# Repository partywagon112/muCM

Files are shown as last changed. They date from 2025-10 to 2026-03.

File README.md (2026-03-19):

# μCM

A small ESP32 based flexible controller, intended for Matter to control an RGB light or motor, but very very flexible. Based around ESP32-C6 for flexibility. Built to work in two contexts, in isolated locations where only power may be provided, up to 40V 3A, or as a PD powered dongle, up to 20V, 3A. 

Includes a 3V3 CAN driver for interacting with smaller devices, two pairs of half bridges allow driving servos, LEDs, or outputs more generally. 

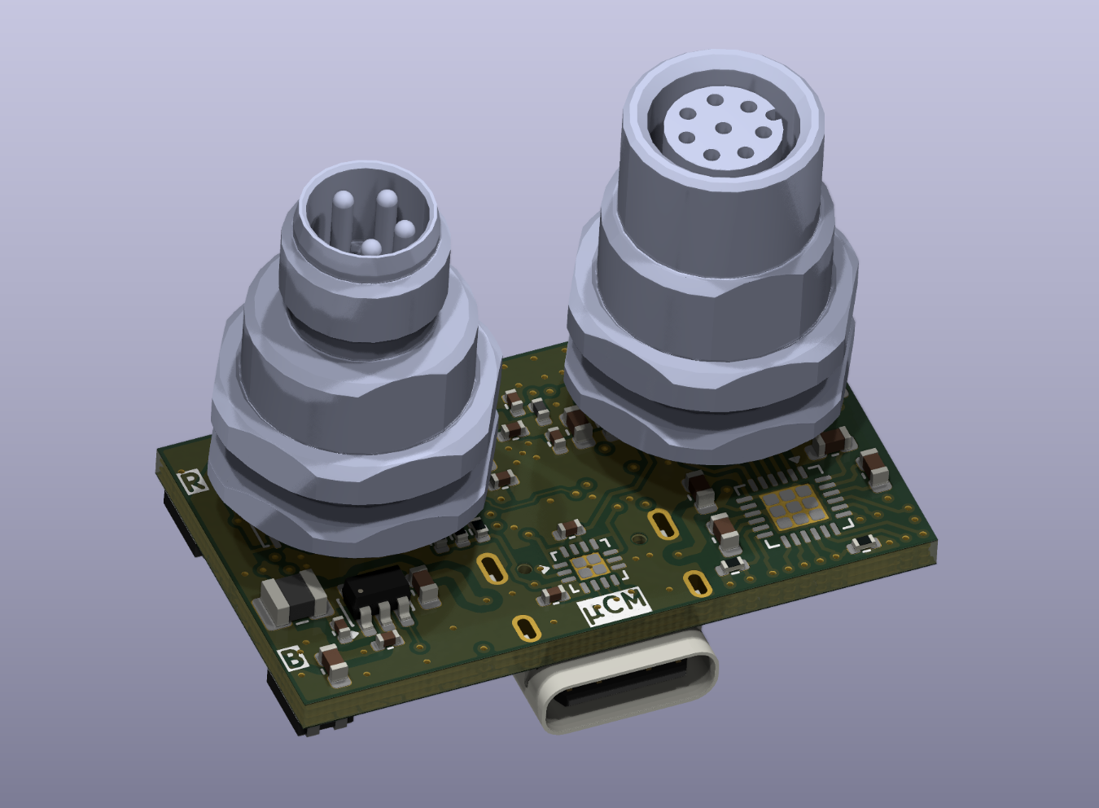
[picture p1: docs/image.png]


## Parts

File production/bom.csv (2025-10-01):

Designator | Footprint | Quantity | Value | LCSC Part #
C1 | 0805 | 1 | 22nF | KAS21KR71H223KU
C10, C11, C12, C14, C7, C9 | 0603 | 6 | 10 nF | GCM188R71H103KA37D
C13, C17, C28, C30, C6, C8 | 0402 | 6 | 100n | GCM155R71H104KE02J
C15, C16 | 0402 | 2 | 5.6n | GCM155R71H562KA55D
C2, C31 | 0603 | 2 | 220nF | GCM188R71H224KA64D
C29 | 0805 | 1 | 10uF | CGA4J1X7S1C106K125AE
C3, C5 | 0805 | 2 | 100n | KAS21KR72A104KU
C4 | 0603 | 1 | 1u | GRT188R61H105KE13D
D1 | SOT-416 | 1 | RCLAMP0582B.TCT | RCLAMP0582B.TCT
D2, D3 | Nexperia_CFP3_SOD-123W | 2 | PMEG60T30ELRX | PMEG60T30ELRX
F1 | 0805 | 1 | 5A | MFU0805FF05000P100
J1 | USB_C_Receptacle_GCT_USB4105-xx-A_16P_TopMnt_Horizontal | 1 | USB4105 | USB4105-GF-A
J2 | JST_PH_S4B-PH-K_1x04_P2.00mm_Horizontal | 1 | S4B-PH-K-S | S4B-PH-K-S
J4 | JST_XH_S2B-XH-A-1_1x02_P2.50mm_Horizontal | 1 | S2B-XH-A-1 | S2B-XH-A-1
J5 | JST_PH_S2B-PH-K_1x02_P2.00mm_Horizontal | 1 | S2B-PH-K-S | S2B-PH-K-S
L2 | 1008 | 1 | 6.8 uH | SRN2510BTA-6R8M
LED1, LED2 | 0603 | 2 | Red | 150060SS75020
R1, R5, R6, R7, R8 | 0402 | 5 | 10k | CR0402AFX-1002GAS
R10, R11, R9 | 0402 | 3 | 4.75k | CR0402AFX-4751GAS
R2, R3 | 0402 | 2 | 2k | CR0402AFX-2001GAS
R4 | 0402 | 1 | 330 kR | CRGCQ0402F330K
SW1, SW2 | SW_Push_1P1T-SH_NO_CK_KMR2xxG | 2 | NO | KMR221G LFS
U1 | WQFN-14-1EP_2.5x2.5mm_P0.5mm_EP1.45x1.45mm | 1 | FUSB302B01MPX | FUSB302B01MPX
U2 | ESP32-S3-WROOM-1 | 1 | ESP32-S3-WROOM-1-N8R8 | ESP32-S3-WROOM-1-N8R8
U3 | VQFN-24-1EP_4x4mm_P0.5mm_EP2.45x2.45mm | 1 | DRV8955 | DRV8955PRGER
U5 | SOT-23-6 | 1 | LMR50410Y3FQDBVRQ1 | LMR50410Y3FQDBVRQ1

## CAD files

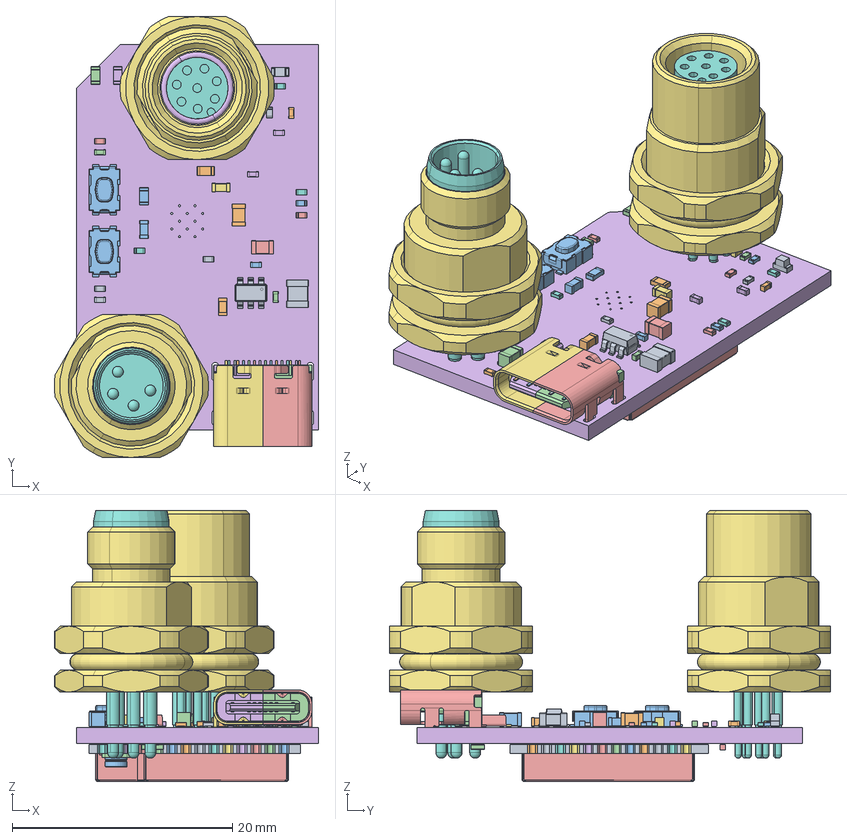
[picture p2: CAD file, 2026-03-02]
housing/MatterRGB_Assy.FCStd
24.0 x 40.0 x 24.6 mm
LED_0603_1608Metric
C_0603_1608Metric
C_0603_1608Metric001
USB_C_Receptacle_GCT_USB4105-xx-A_16P_TopMnt_Horizontal
USB_C_Receptacle_GCT_USB4105-xx-A_16P_TopMnt_Horizontal001
USB_C_Receptacle_GCT_USB4105-xx-A_16P_TopMnt_Horizontal002
USB_C_Receptacle_GCT_USB4105-xx-A_16P_TopMnt_Horizontal003
USB_C_Receptacle_GCT_USB4105-xx-A_16P_TopMnt_Horizontal004
USB_C_Receptacle_GCT_USB4105-xx-A_16P_TopMnt_Horizontal005
USB_C_Receptacle_GCT_USB4105-xx-A_16P_TopMnt_Horizontal006
USB_C_Receptacle_GCT_USB4105-xx-A_16P_TopMnt_Horizontal007
USB_C_Receptacle_GCT_USB4105-xx-A_16P_TopMnt_Horizontal008
USB_C_Receptacle_GCT_USB4105-xx-A_16P_TopMnt_Horizontal009
USB_C_Receptacle_GCT_USB4105-xx-A_16P_TopMnt_Horizontal010
USB_C_Receptacle_GCT_USB4105-xx-A_16P_TopMnt_Horizontal011
USB_C_Receptacle_GCT_USB4105-xx-A_16P_TopMnt_Horizontal012
USB_C_Receptacle_GCT_USB4105-xx-A_16P_TopMnt_Horizontal013
USB_C_Receptacle_GCT_USB4105-xx-A_16P_TopMnt_Horizontal014
USB_C_Receptacle_GCT_USB4105-xx-A_16P_TopMnt_Horizontal015
USB_C_Receptacle_GCT_USB4105-xx-A_16P_TopMnt_Horizontal016
USB_C_Receptacle_GCT_USB4105-xx-A_16P_TopMnt_Horizontal017
USB_C_Receptacle_GCT_USB4105-xx-A_16P_TopMnt_Horizontal018
USB_C_Receptacle_GCT_USB4105-xx-A_16P_TopMnt_Horizontal019
USB_C_Receptacle_GCT_USB4105-xx-A_16P_TopMnt_Horizontal020
USB_C_Receptacle_GCT_USB4105-xx-A_16P_TopMnt_Horizontal021
USB_C_Receptacle_GCT_USB4105-xx-A_16P_TopMnt_Horizontal022
USB_C_Receptacle_GCT_USB4105-xx-A_16P_TopMnt_Horizontal023
USB_C_Receptacle_GCT_USB4105-xx-A_16P_TopMnt_Horizontal024
USB_C_Receptacle_GCT_USB4105-xx-A_16P_TopMnt_Horizontal025
USB_C_Receptacle_GCT_USB4105-xx-A_16P_TopMnt_Horizontal026
USB_C_Receptacle_GCT_USB4105-xx-A_16P_TopMnt_Horizontal027
USB_C_Receptacle_GCT_USB4105-xx-A_16P_TopMnt_Horizontal028
USB_C_Receptacle_GCT_USB4105-xx-A_16P_TopMnt_Horizontal029
USB_C_Receptacle_GCT_USB4105-xx-A_16P_TopMnt_Horizontal030
USB_C_Receptacle_GCT_USB4105-xx-A_16P_TopMnt_Horizontal031
USB_C_Receptacle_GCT_USB4105-xx-A_16P_TopMnt_Horizontal032
USB_C_Receptacle_GCT_USB4105-xx-A_16P_TopMnt_Horizontal033
USB_C_Receptacle_GCT_USB4105-xx-A_16P_TopMnt_Horizontal034
USB_C_Receptacle_GCT_USB4105-xx-A_16P_TopMnt_Horizontal035
R_0402_1005Metric
C_0402_1005Metric
C_0805_2012Metric
R_0402_1005Metric001
R_0603_1608Metric
R_0402_1005Metric002
C_0402_1005Metric001
CDM806 HOUSING
M8_PINS_MALE_FRONT_4P
L_1008_2520Metric
R_0603_1608Metric001
R_0402_1005Metric003
R_0402_1005Metric004
R_0402_1005Metric005
R_0603_1608Metric002
C_0402_1005Metric002
R_0402_1005Metric006
SOT-23-6
R_0402_1005Metric007
SW_Push_1P1T-SH_NO_CK_KMR2xxG
C_0805_2012Metric001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

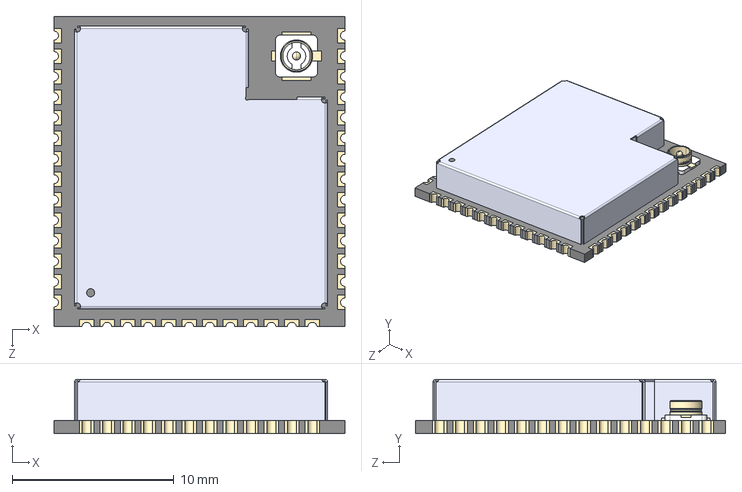
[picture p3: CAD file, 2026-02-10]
hardware/3d/ESP32-S3-WROOM-1U-N8R8--3DModel-STEP-56544.STEP
18.0 x 3.35 x 19.2 mm

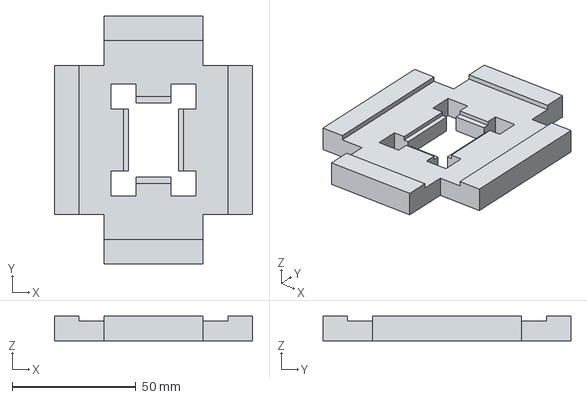
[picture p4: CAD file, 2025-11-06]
production/stencil_holder-Body.step
80.0 x 100.0 x 10.0 mm

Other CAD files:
housing/MatterRGB.step
production/stencil_holder.FCStd

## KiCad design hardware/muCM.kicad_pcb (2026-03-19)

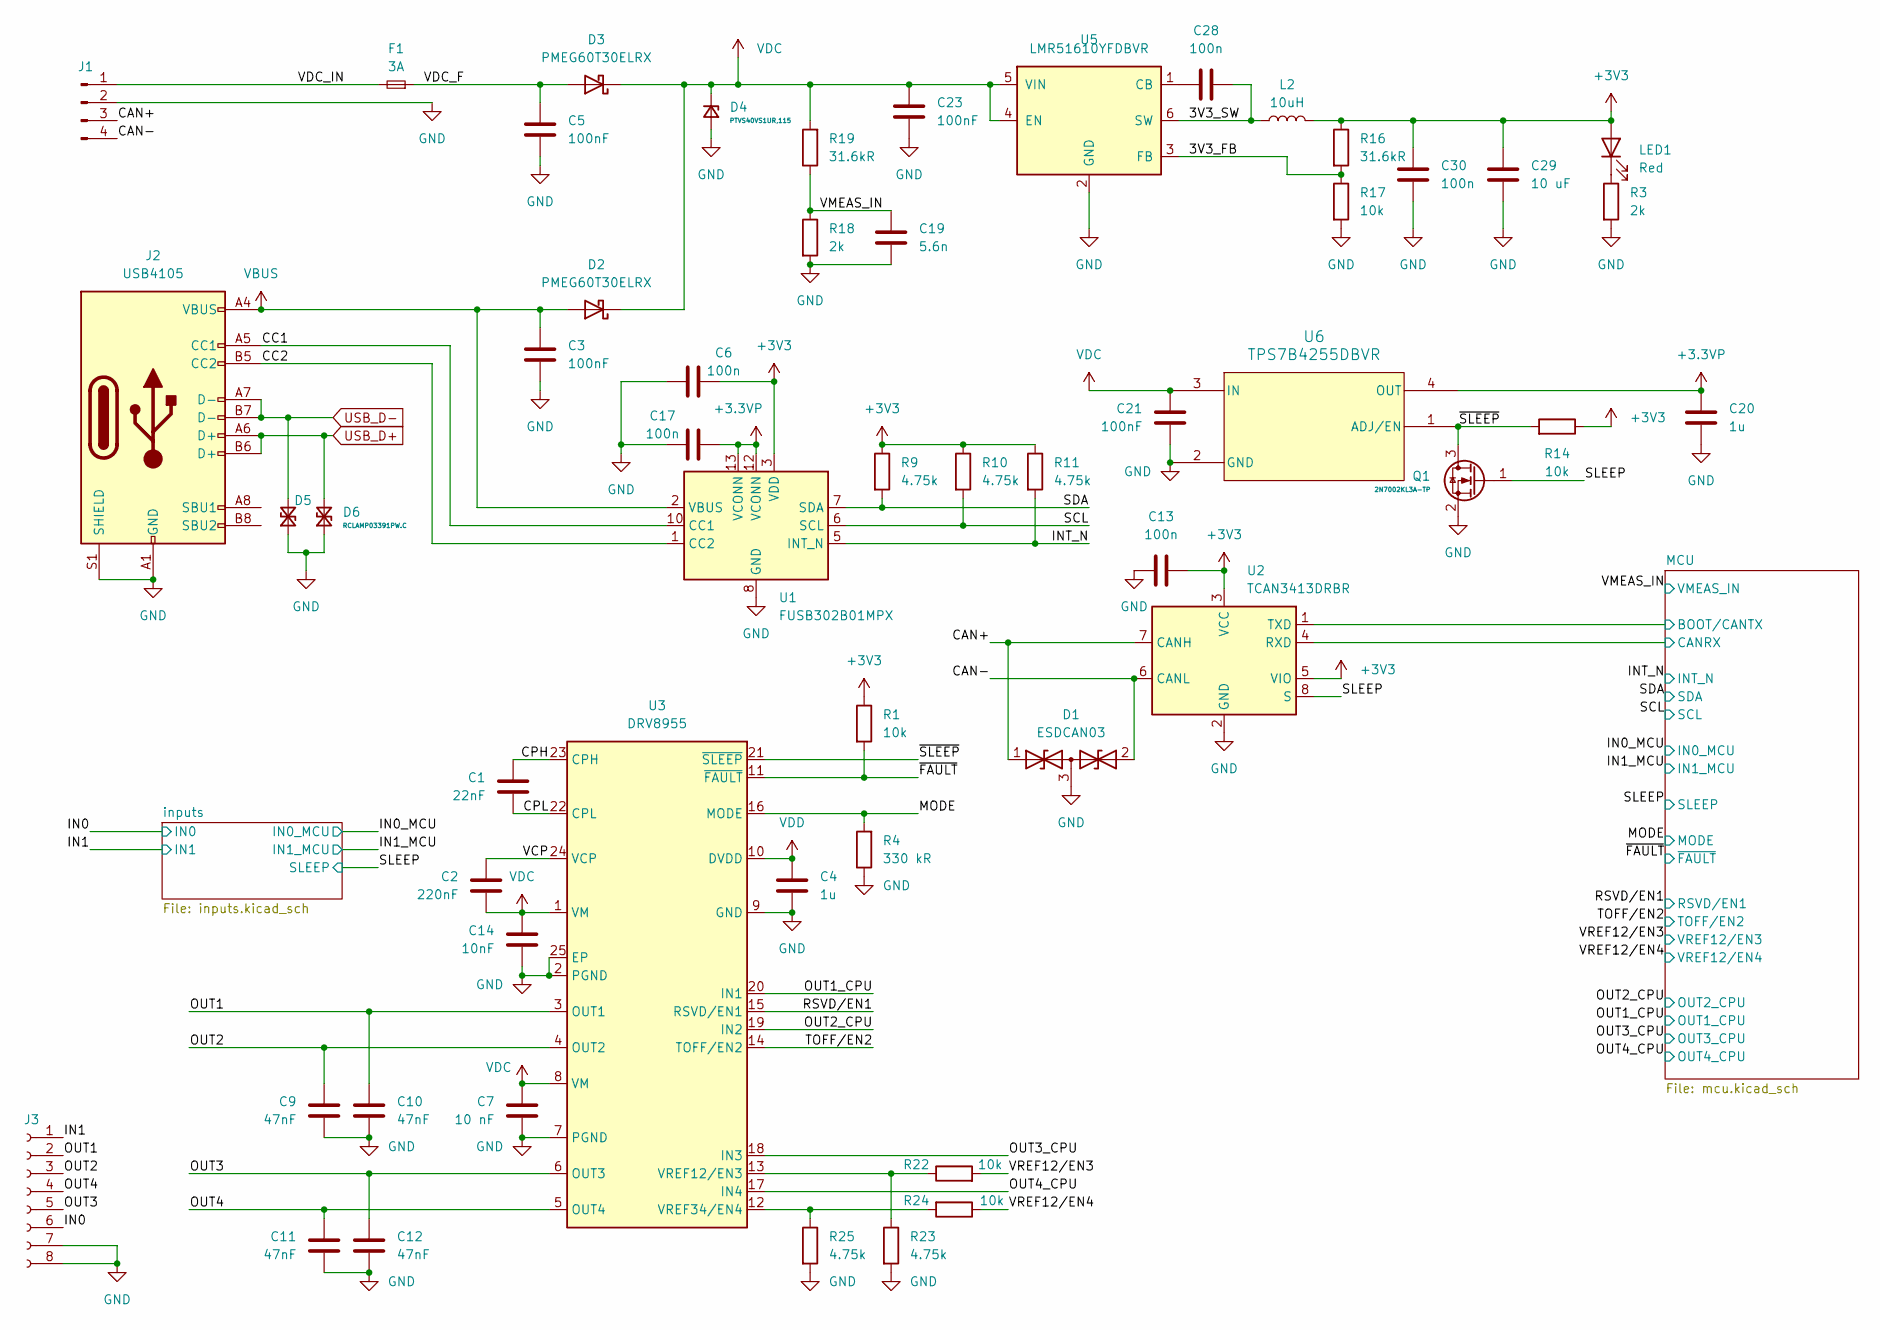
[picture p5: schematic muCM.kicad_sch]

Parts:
C1: 22nF; C_0603_1608Metric; MPN CL10B223KC8WPNC; DigiKey SPN 1276-CL10B223KC8WPNCCT-ND
C2: 220nF; C_0603_1608Metric; MPN HMK107C7224MAHTE; DigiKey SPN 587-5013-1-ND
C3, C5, C21, C23: 100nF; C_0603_1608Metric; MPN GCJ188R72A104KA01D; DigiKey SPN 490-13420-1-ND
C4, C20: 1u; C_0603_1608Metric; MPN GRT188R61H105KE13D; DigiKey SPN 490-12330-1-ND
C6, C13, C17, C28, C30: 100n; C_0402_1005Metric; MPN GCM155R71H104KE02J
C7: 10 nF; R_0603_1608Metric; MPN GCM188R71H103KA37D; DigiKey SPN 490-4778-1-ND
C9, C10, C11, C12: 47nF; C_0603_1608Metric; MPN CGA3E3X7S2A473K080AE; DigiKey SPN 445-173702-1-ND
C14: 10nF; C_0603_1608Metric; MPN CL10B103KC8WPNC; DigiKey SPN 1276-6556-1-ND
C19: 5.6n; C_0402_1005Metric; MPN GCM155R71H562KA55D; DigiKey SPN 490-GCM155R71H562KA55DCT-ND
C29: 10 uF; C_0603_1608Metric; MPN GRT188R61E106ME13D; DigiKey SPN 490-12323-1-ND
D1: ESDCAN03; DFN1006-3; MPN ESDCAN03-2BM3Y; DigiKey SPN 497-ESDCAN03-2BM3YCT-ND
D2, D3: PMEG60T30ELRX; Nexperia_CFP3_SOD-123W; MPN PMEG60T30ELRX; DigiKey SPN 1727-7806-1-ND
D4: PTVS40VS1UR,115; Nexperia_CFP3_SOD-123W; MPN PTVS40VS1UR,115; DigiKey SPN 1727-5873-1-ND
D5, D6: RCLAMP03391PW.C; D_SOD-882; MPN RCLAMP03391PW.C; DigiKey SPN 600-RCLAMP03391PW.CCT-ND
F1: 3A; Fuse_0805_2012Metric; MPN MFU0805FF03000P100; DigiKey SPN MFU08053.00CT-ND
J1: CDM806-04A-MP-F011-67; CUI_CDM806-04A-MP-F011-67; MPN CDM806-04A-MP-F011-67; DigiKey SPN 2223-CDM806-04A-MP-F011-67-ND
J2: USB4105; USB_C_Receptacle_GCT_USB4105-xx-A_16P_TopMnt_Horizontal; MPN USB4105-GF-A; DigiKey SPN 2073-USB4105-GF-ACT-ND
J3: CDM805-08A-FP-F011-67; CUI_CDM805-08A-FP-F011-67; MPN CDM805-08A-FP-F011-67; DigiKey SPN 2223-CDM805-08A-FP-F011-67-ND
L2: 10uH; L_1008_2520Metric; MPN SRN2510BTA-100M; DigiKey SPN 118-SRN2510BTA-100MCT-ND
LED1: Red; LED_0603_1608Metric; MPN 150060SS75020
Q1: 2N7002KL3A-TP; Diodes_DFN1006-3; MPN 2N7002KL3A-TP; DigiKey SPN 353-2N7002KL3A-TPCT-ND
R1, R14, R17, R22, R24: 10k; R_0402_1005Metric; MPN CR0402AFX-1002GAS; DigiKey SPN CR0402AFX-1002GASCT-ND
R3, R18: 2k; R_0402_1005Metric; MPN CR0402AFX-2001GAS
R4: 330 kR; R_0402_1005Metric; MPN CRGCQ0402F330K; DigiKey SPN A129657CT-ND
R9, R10, R11, R23, R25: 4.75k; R_0402_1005Metric; MPN CR0402AFX-4751GAS; DigiKey SPN CR0402AFX-4751GASCT-ND
R16, R19: 31.6kR; R_0402_1005Metric; MPN CRCW040231K6FKED; DigiKey SPN 541-31.6KLCT-ND
U1: FUSB302B01MPX; WQFN-14-1EP_2.5x2.5mm_P0.5mm_EP1.45x1.45mm; MPN FUSB302B01MPX; DigiKey SPN FUSB302B01MPXCT-ND
U2: TCAN3413DRBR; VSON-8-1EP_3x3mm_P0.65mm_EP1.6x2.4mm; MPN TCAN3413DRBR; DigiKey SPN 296-TCAN3413DRBRCT-ND
U3: DRV8955; VQFN-24-1EP_4x4mm_P0.5mm_EP2.45x2.45mm; MPN DRV8955PRGER; DigiKey SPN 296-DRV8955PRGERCT-ND
U5: LMR51610YFDBVR; SOT-23-6; MPN LMR51610YFDBVR; DigiKey SPN 296-LMR51610YFDBVRCT-ND
U6: TPS7B4255DBVR; SOT-23-5; MPN TPS7B4255DBVR; DigiKey SPN 296-TPS7B4255DBVRCT-ND

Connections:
+3.3VP: C17.1, C20.1, U1.12 (VCONN), U1.13 (VCONN), U6.4 (OUT); also elsewhere on the board
+3V3: C6.1, C13.2, C29.1, C30.1, L2.2, LED1.2 (A), R1.1, R9.1, R10.1, R11.1, R14.1, R16.1, U1.3 (VDD), U1.4 (VDD), U2.3 (VCC), U2.5 (VIO); also elsewhere on the board
/3V3_FB: R16.2, R17.1, U5.3 (FB)
/3V3_SW: C28.2, L2.1, U5.6 (SW)
/CAN+: D1.1 (A1), J1.3, U2.7 (CANH)
/CAN-: D1.2 (A2), J1.4, U2.6 (CANL)
/CC1: J2.A5 (CC1), U1.10 (CC1), U1.11 (CC1)
/CC2: J2.B5 (CC2), U1.1 (CC2), U1.14 (CC2)
/CPH: C1.1, U3.23 (CPH)
/CPL: C1.2, U3.22 (CPL)
/IN0: J3.6; also elsewhere on the board
/IN1: J3.1; also elsewhere on the board
/INT_N: R11.2, U1.5 (INT_N); also elsewhere on the board
/MCU/BOOT/CANTX: U2.1 (TXD); also elsewhere on the board
/MCU/CANRX: U2.4 (RXD); also elsewhere on the board
/MODE: R4.2, U3.16 (MODE); also elsewhere on the board
/OUT1: C10.1, J3.2, U3.3 (OUT1)
/OUT1_CPU: U3.20 (IN1); also elsewhere on the board
/OUT2: C9.1, J3.3, U3.4 (OUT2)
/OUT2_CPU: U3.19 (IN2); also elsewhere on the board
/OUT3: C12.1, J3.5, U3.6 (OUT3)
/OUT3_CPU: U3.18 (IN3); also elsewhere on the board
/OUT4: C11.1, J3.4, U3.5 (OUT4)
/OUT4_CPU: U3.17 (IN4); also elsewhere on the board
/RSVD/EN1: U3.15 (RSVD/EN1); also elsewhere on the board
/SCL: R10.2, U1.6 (SCL); also elsewhere on the board
/SDA: R9.2, U1.7 (SDA); also elsewhere on the board
/SLEEP: Q1.1 (G), U2.8 (S); also elsewhere on the board
/TOFF/EN2: U3.14 (TOFF/EN2); also elsewhere on the board
/VCP: C2.1, U3.24 (VCP)
/VDC_F: C5.1, D3.2 (A), F1.1
/VDC_IN: F1.2, J1.1
/VMEAS_IN: C19.1, R18.1, R19.1; also elsewhere on the board
/VREF12/EN3: R22.2; also elsewhere on the board
/VREF12/EN4: R24.1; also elsewhere on the board
/~FAULT: R1.2, U3.11 (~FAULT); also elsewhere on the board
/~SLEEP: Q1.3 (D), R14.2, U3.21 (~SLEEP), U6.1 (ADJ/EN)
GND: C3.2, C4.2, C5.2, C6.2, C7.2, C9.2, C10.2, C11.2, C12.2, C13.1, C14.2, C17.2, C19.2, C20.2, C21.2, C23.2, C29.2, C30.2, D1.3 (common), D4.2 (A), D5.1 (A1), D6.1 (A1), J1.2, J2.A1 (GND), J2.A12 (GND), J2.B1 (GND), J2.B12 (GND), J2.S1 (SHIELD), J3.7, J3.8, Q1.2 (S), R3.2, R4.1, R17.2, R18.2, R23.2, R25.2, U1.8 (GND), U1.9 (GND), U1.15 (GND), U2.2 (GND), U2.9, U3.2 (PGND), U3.7 (PGND), U3.9 (GND), U3.25 (EP), U5.2 (GND), U6.2 (GND); also elsewhere on the board
unnamed: LED1.1 (K), R3.1
unnamed: R22.1, R23.1, U3.13 (VREF12/EN3)
unnamed: R24.2, R25.1, U3.12 (VREF34/EN4)
unnamed: C28.1, U5.1 (CB)
USB_D+: D6.2 (A2), J2.A6 (D+), J2.B6 (D+); also elsewhere on the board
USB_D-: D5.2 (A2), J2.A7 (D-), J2.B7 (D-); also elsewhere on the board
VBUS: C3.1, D2.2 (A), J2.A4 (VBUS), J2.A9 (VBUS), J2.B4 (VBUS), J2.B9 (VBUS), U1.2 (VBUS)
VDC: C2.2, C7.1, C14.1, C21.1, C23.1, D2.1 (K), D3.1 (K), D4.1 (K), R19.2, U3.1 (VM), U3.8 (VM), U5.4 (EN), U5.5 (VIN), U6.3 (IN)
VDD: C4.1, U3.10 (DVDD)

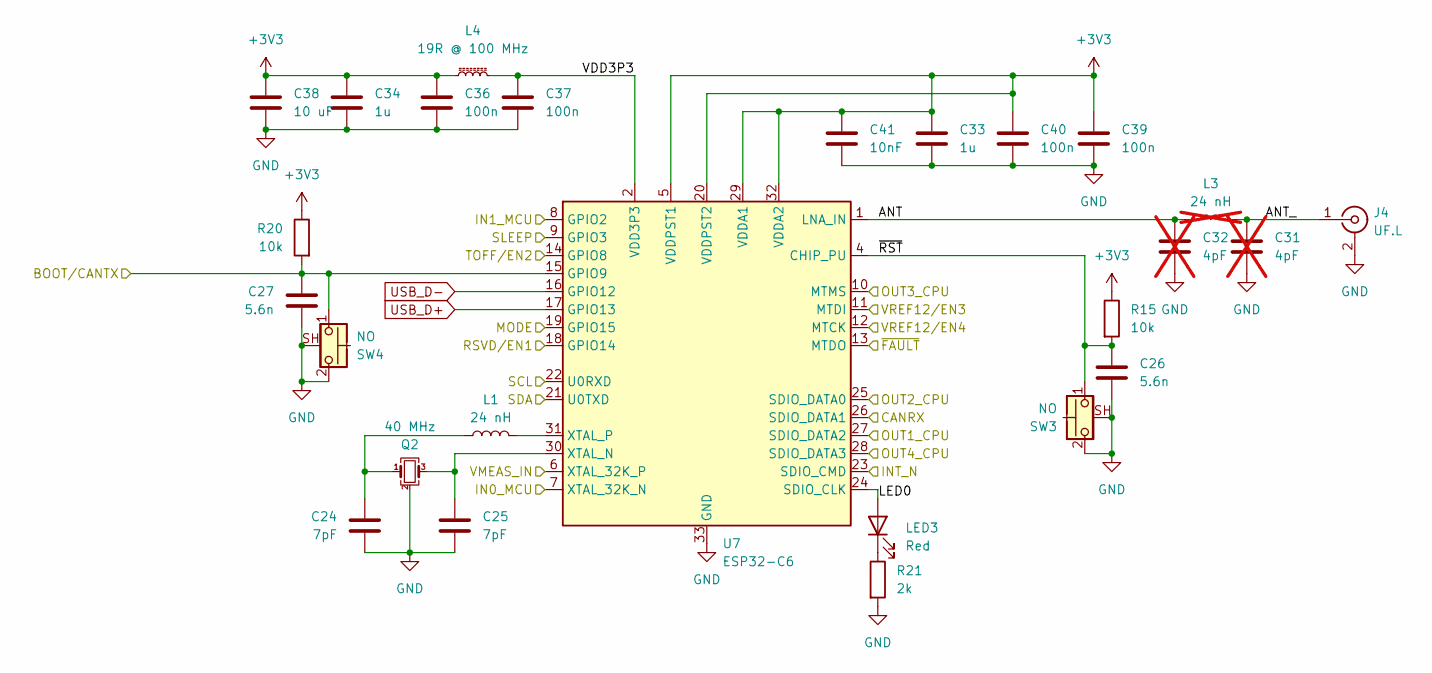
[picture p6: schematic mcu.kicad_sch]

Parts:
C24, C25: 7pF; C_0402_1005Metric; MPN GCM1555C1H7R0BA16D; DigiKey SPN 490-GCM1555C1H7R0BA16DCT-ND
C26, C27: 5.6n; C_0402_1005Metric; MPN GCM155R71H562KA55D; DigiKey SPN 490-GCM155R71H562KA55DCT-ND
C31, C32: 4pF; C_0402_1005Metric; MPN GCM1555C1H4R0BA16D; DigiKey SPN 490-GCM1555C1H4R0BA16DCT-ND; not fitted
C33, C34: 1u; C_0603_1608Metric; MPN GRT188R61H105KE13D; DigiKey SPN 490-12330-1-ND
C36, C37, C39, C40: 100n; C_0402_1005Metric; MPN GCM155R71H104KE02J
C38: 10 uF; C_0603_1608Metric; MPN GRT188R61E106ME13D; DigiKey SPN 490-12323-1-ND
C41: 10nF; C_0402_1005Metric; MPN GCM155R71H103KA55D; DigiKey SPN 490-4762-1-ND
J4: UF.L; U.FL_Hirose_U.FL-R-SMT-1_Vertical; MPN U.FL-R-SMT(10); DigiKey SPN H9161CT-ND
L1: 24 nH; L_0402_1005Metric; MPN MLG1005S24NJTD25; DigiKey SPN 445-16275-1-ND
L3: 24 nH; L_0402_1005Metric; MPN MLG1005S24NJTD25; DigiKey SPN 445-16275-1-ND; not fitted
L4: 19R @ 100 MHz; L_0402_1005Metric; MPN LI0402E190R-10; DigiKey SPN 240-LI0402E190R-10CT-ND
LED3: Red; LED_0603_1608Metric; MPN 150060SS75020
Q2: 40 MHz; Crystal_SMD_2016-4Pin_2.0x1.6mm; MPN XTL501100-M118-207; DigiKey SPN 3994-XTL501100-M118-207CT-ND
R15, R20: 10k; R_0402_1005Metric; MPN CR0402AFX-1002GAS; DigiKey SPN CR0402AFX-1002GASCT-ND
R21: 2k; R_0402_1005Metric; MPN CR0402AFX-2001GAS
SW3, SW4: NO; SW_Push_1P1T-SH_NO_CK_KMR2xxG; MPN KMR221G LFS; DigiKey SPN 401-1427-1-ND
U7: ESP32-C6; QFN-32-1EP_5x5mm_P0.5mm_EP3.7x3.7mm; MPN ESP32-C6FH4; DigiKey SPN 1904-ESP32-C6FH4CT-ND

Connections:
+3V3: C33.1, C34.1, C36.1, C38.1, C39.1, C40.1, C41.1, L4.1, R15.1, R20.1, U7.5 (VDDPST1), U7.20 (VDDPST2), U7.29 (VDDA1), U7.32 (VDDA2); also elsewhere on the board
/IN0_MCU: U7.7 (XTAL_32K_N); also elsewhere on the board
/IN1_MCU: U7.8 (GPIO2); also elsewhere on the board
/INT_N: U7.23 (SDIO_CMD); also elsewhere on the board
/MCU/ANT: C32.1, L3.1, U7.1 (LNA_IN)
/MCU/ANT_: C31.1, J4.1 (In), L3.2
/MCU/BOOT/CANTX: C27.1, R20.2, SW4.1, U7.15 (GPIO9); also elsewhere on the board
/MCU/CANRX: U7.26 (SDIO_DATA1); also elsewhere on the board
/MCU/LED0: LED3.2 (A), U7.24 (SDIO_CLK)
/MCU/~RST: C26.1, R15.2, SW3.1, U7.4 (CHIP_PU)
/MODE: U7.19 (GPIO15); also elsewhere on the board
/OUT1_CPU: U7.27 (SDIO_DATA2); also elsewhere on the board
/OUT2_CPU: U7.25 (SDIO_DATA0); also elsewhere on the board
/OUT3_CPU: U7.10 (MTMS); also elsewhere on the board
/OUT4_CPU: U7.28 (SDIO_DATA3); also elsewhere on the board
/RSVD/EN1: U7.18 (GPIO14); also elsewhere on the board
/SCL: U7.22 (U0RXD); also elsewhere on the board
/SDA: U7.21 (U0TXD); also elsewhere on the board
/SLEEP: U7.9 (GPIO3); also elsewhere on the board
/TOFF/EN2: U7.14 (GPIO8); also elsewhere on the board
/VMEAS_IN: U7.6 (XTAL_32K_P); also elsewhere on the board
/VREF12/EN3: U7.11 (MTDI); also elsewhere on the board
/VREF12/EN4: U7.12 (MTCK); also elsewhere on the board
/~FAULT: U7.13 (MTDO); also elsewhere on the board
GND: C24.2, C25.2, C26.2, C27.2, C31.2, C32.2, C33.2, C34.2, C36.2, C37.2, C38.2, C39.2, C40.2, C41.2, J4.2 (Ext), Q2.2 (G), Q2.4 (G), R21.2, SW3.2, SW3.SH (B), SW4.2, SW4.SH (B), U7.33 (GND); also elsewhere on the board
unnamed: C24.1, L1.1, Q2.1
unnamed: LED3.1 (K), R21.1
unnamed: C25.1, Q2.3, U7.30 (XTAL_N)
unnamed: L1.2, U7.31 (XTAL_P)
USB_D+: U7.17 (GPIO13); also elsewhere on the board
USB_D-: U7.16 (GPIO12); also elsewhere on the board
VDD3P3: C37.1, L4.2, U7.2 (VDD3P3), U7.3 (VDD3P3)

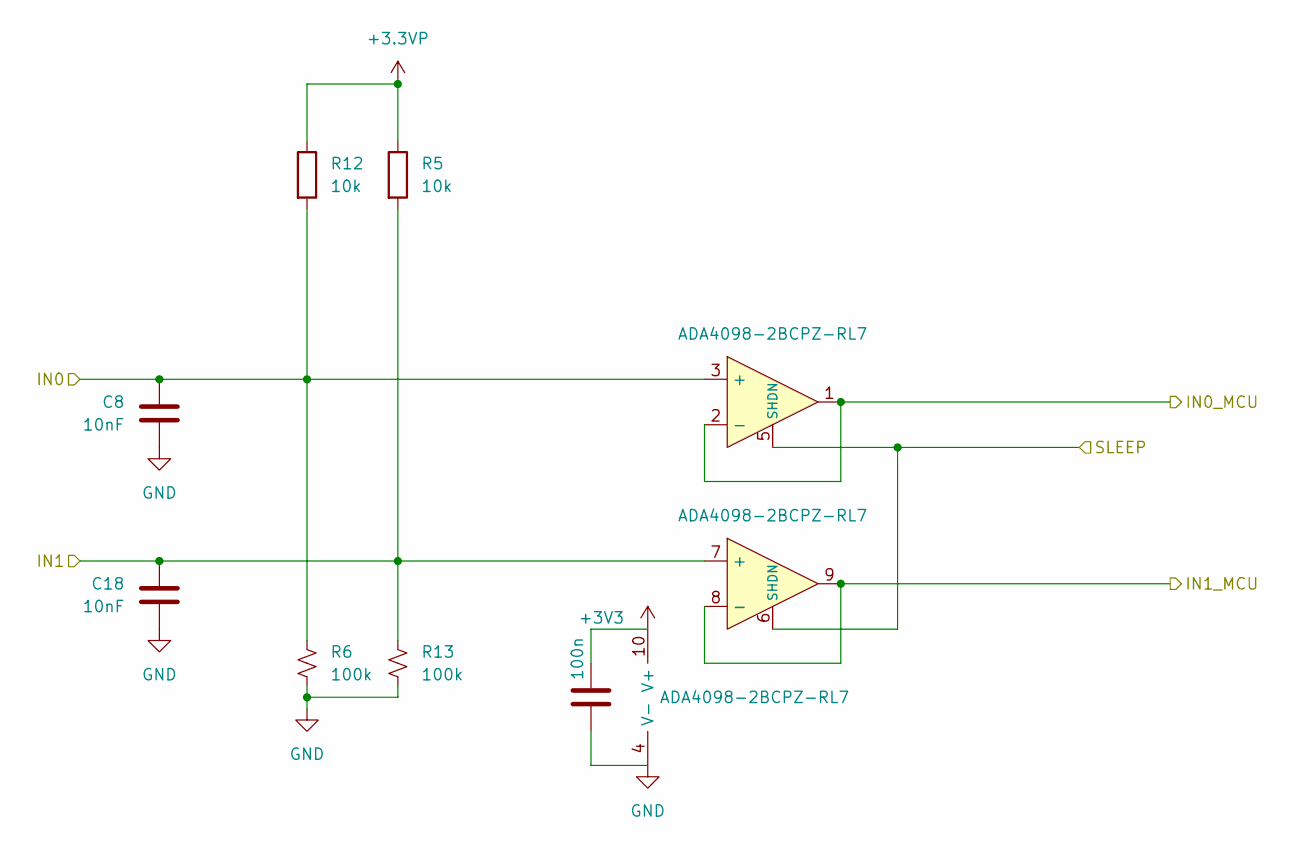
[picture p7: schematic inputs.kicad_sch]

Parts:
C8, C18: 10nF; C_0603_1608Metric; MPN CL10B103KC8WPNC; DigiKey SPN 1276-6556-1-ND
C22: 100n; C_0402_1005Metric; MPN GCM155R71H104KE02J
R5, R12: 10k; R_0402_1005Metric; MPN CR0402AFX-1002GAS; DigiKey SPN CR0402AFX-1002GASCT-ND
R6, R13: 100k; R_0402_1005Metric
U4: ADA4098-2BCPZ-RL7; LFCSP-WD-10-1EP_3x3mm_P0.5mm_EP1.64x2.38mm; MPN ADA4098-2BCPZ-RL7; DigiKey SPN 505-ADA4098-2BCPZ-RL7TR-ND

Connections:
+3.3VP: R5.1, R12.1; also elsewhere on the board
+3V3: C22.1, U4.10 (V+); also elsewhere on the board
/IN0: C8.1, R6.2, R12.2, U4.3 (+); also elsewhere on the board
/IN0_MCU: U4.1, U4.2 (-); also elsewhere on the board
/IN1: C18.1, R5.2, R13.2, U4.7 (+); also elsewhere on the board
/IN1_MCU: U4.8 (-), U4.9; also elsewhere on the board
/SLEEP: U4.5 (SHDN), U4.6 (SHDN); also elsewhere on the board
GND: C8.2, C18.2, C22.2, R6.1, R13.1, U4.4 (V-), U4.11 (V-); also elsewhere on the board

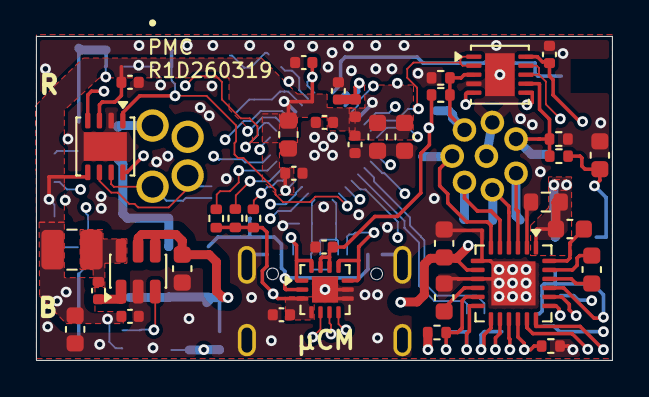
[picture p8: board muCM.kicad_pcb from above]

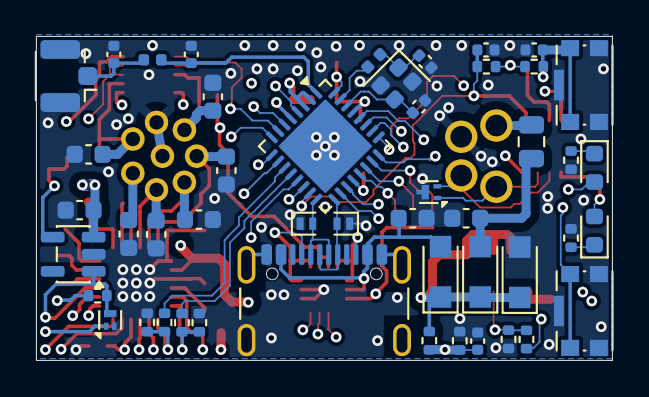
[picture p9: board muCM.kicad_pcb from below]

Board: 4 copper layers, 32.0 x 18.0 mm, 88 parts (48 on the bottom side), 58 nets.

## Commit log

2025-10-30 Added stencil
    [stencil_holder-Body.step, stencil_holder.FCStd]
2025-11-06 Lots of other stuff
    [MatterRGB.kicad_sch, stencil_holder-Body.step, stencil_holder.FCStd]
2025-11-11 fixed typos in driver
2026-02-10 Added new connector/mounting strategy
    [ESP32-S3-WROOM-1U-N8R8--3DModel-STEP-56544.STEP, MatterRGB.kicad_pcb, MatterRGB.kicad_sch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]
2026-03-02 Last version before c6 conversion
    [ESP32-S3-WROOM-1U-N8R8--3DModel-STEP-56544.STEP, MatterRGB.kicad_pcb, MatterRGB.kicad_sch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]
2026-03-18 Finished draft layout of muCM update.
    [MatterRGB.kicad_pcb, MatterRGB.kicad_sch, inputs.kicad_sch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]
2026-03-19 removed backups
    [MatterRGB.kicad_pcb, MatterRGB.kicad_sch, calculations.ods]
2026-03-19 Rename project to μCM and refine description
    Updated project name and enhanced description for clarity.
2026-03-19 Enhance README with detailed controller specifications
    Expanded description of the μCM controller's capabilities and power contexts.
